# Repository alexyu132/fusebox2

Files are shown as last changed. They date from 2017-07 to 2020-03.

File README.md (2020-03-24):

# FuseBox2/FuseBox2R
A new CoreXY 3D printer design. This design has 2 variants:

* FuseBox2R: An improved version using an MGN12 linear rail gantry.
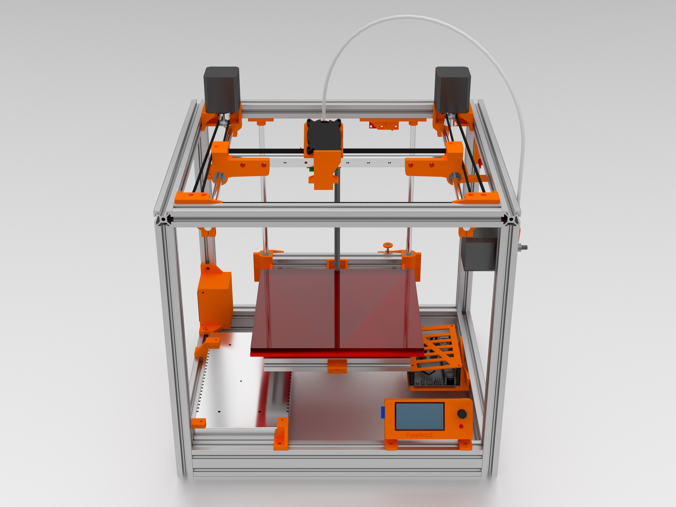
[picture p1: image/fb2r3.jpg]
FuseBox2R Render


* FuseBox2: The original design using a dual 8mm rod gantry.

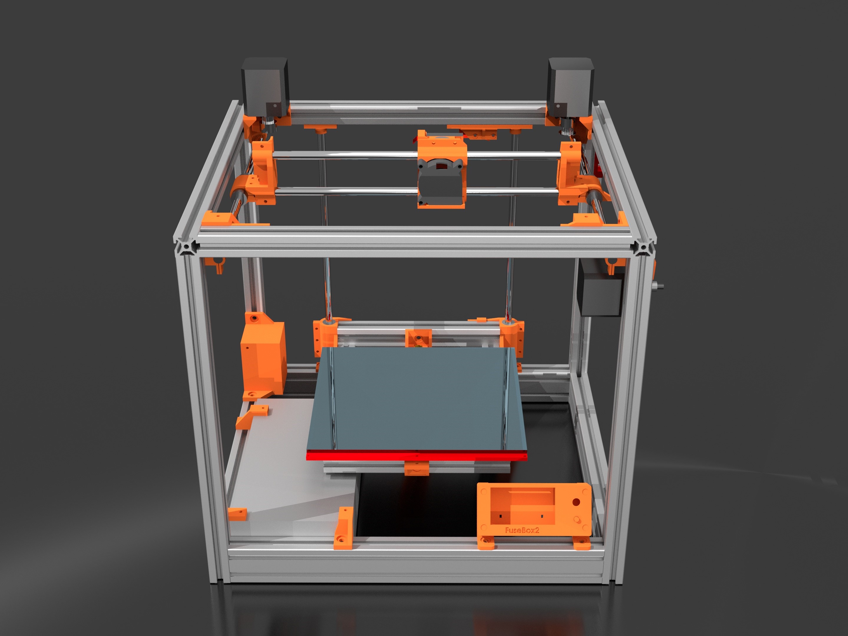
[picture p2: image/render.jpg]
FuseBox2 Render


## Specifications
* Rigid 2020(top and sides)/2040(bottom) aluminum extrusion frame
* Non-crossing CoreXY belt path
* 210x200x210mm (FuseBox2) or 210x205x210mm (FuseBox2R) build area
* 390x340x412mm size
* PCB heatbed with 3 point leveling
* Powerful 2040 part cooling blower
* E3D V6 compatible hotend + Bowden extruder
* 24v + 32 bit electronics recommended - SKR 1.3 and Duet are good options

## Improvements over original FuseBox
* Slightly more compact
* Slightly larger build area
* Much greater frame and z axis rigidity
* Belt tensioning improvements - much easier to tension; screw-clamped to prevent slipping out
* Clamped bearing and rod mounts - no more structural zip ties
* Proper belt idlers instead of 625 bearings - eliminates belt rubbing
* Extrusions (optionally) joined via tapped ends + screws instead of corner brackets
* Lowered part count
* Better endstop mounting

# Variants

## FuseBox2 v1.0.1

* Minor change from 1.0 - added adjustment screw for more precise Z offset adjustment. Eliminates 2 M5x8mm screws and t-nuts, and needs 1 additional M3x25mm (or longer) bolt and 2 additional M3 lock nuts.

## FuseBox2R v1.1
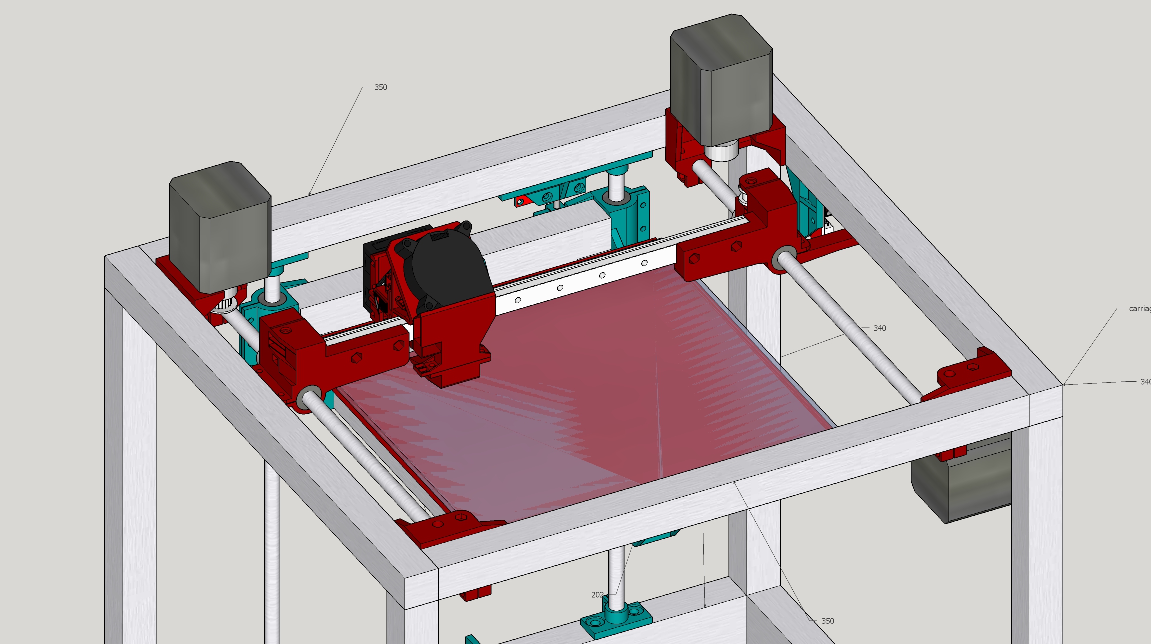
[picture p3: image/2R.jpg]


Switches out the twin 8mm rods on the gantry for a single MGN12 rail. Improvements include 30% gantry weight savings for less ringing and higher speeds, lowered bearing noise, easier belt tensioning, and a modular fan duct. Relatively inexpensive ($10-$15) MGN12 rails can be found on Aliexpress, so it's recommended to build this configuration if starting from scratch. The printed parts for the 2R gantry are in the rail gantry subfolder in the stl folder. Don't print anything from the stock gantry folder if building the rail gantry version, and vice versa.

### Changes from FuseBox2
The entire CoreXY movement will need to be changed out. This includes all the parts on the gantry itself as well as the motor mounts and idler blocks.

Compared to the stock gantry, the belts may need to be shortened slightly.

### Changes in FuseBox2R v1.1

Revised XY movement to simplify assembly and address issues with v1.0 rail gantry:

- X-end rigidity improvements
- Belts moved closer to centerline of MGN rail - alleviates x-end bending from belt tension; should further reduce ringing
- Corner idler brackets made more robust and compact - allows for a few mm more Y travel
- Homing direction reverted to x-min
- Thicker, more rigid 8mm rod holders with looser unclamped fit for easier rod installation

# BOM

| Item | Quantity  |
|---|---|
| **Extrusions**  |
| 2020 extrusion, 350mm | 2  |
| 2020 extrusion, 340mm | 6  |
| 2020 extrusion, 184mm | 1  |
| 2020 extrusion, 202mm | 2  |
| 2040 extrusion, 184mm | 1  |
| 2040 extrusion, 350mm | 2  |
| 2040 extrusion, 300mm | 2  |
| **Heaters, motors, electronics**  |
| MK2 compatible PCB heatbed | 1  |
| Thermistor for heatbed | 1  |
| 15A 24v PSU or 30A 12v PSU | 1  |
| E3DV6 compatible hotend with PTFE tube and coupler | 1  |
| Any electronics (32 bit preferred, mounts available for azsmz board+lcd) | 1  |
| NEMA 17 stepper (60+ oz in/42+ N cm preferred) | 3  |
| NEMA 17 short body stepper (up to 30mm motor body length) | 1  |
| IEC socket with fuse and switch | 1  |
| ~5A 250v fuse | 1  |
| IEC power cord | 1  |
| Mechanical endstop (Note: cut off the microswitch from one endstop to use on the x axis) | 3  |
| 40mm axial fan | 1  |
| 2040 radial blower | 1  |
| **Mechanical**  |
| 8mm OD smooth rod, 300mm length | 6  |
| LM8LUU linear bearing | 6  |
| T8 leadscrew+nut, 250mm length, 2mm pitch preferred | 1  |
| 16T GT2 idler for 6mm belt - 6 toothed/2 smooth (recommended) or all smooth | 8  |
| 20T GT2 pulley for 6mm belt | 2  |
| 3m GT2 belt, 6mm | 1  |
| 625zz bearing | 1  |
| 5mm to 8mm flex coupler | 1  |
| MK8 extruder gear | 1  |
| **Fasteners and other hardware**  |
| M5x8mm button head bolt | 49  |
| M5x12mm button head bolt | 28  |
| M5 T nuts (drop-in recommended) | 49  |
| M3x8mm socket head bolt | 16  |
| M3x10mm button head bolt | 36  |
| M3x25mm button head bolt | 14  |
| Bed leveling spring, nut, and bolt set | 3  |
| Extruder spring | 1  |
| M3 lock nut | 50  |
| Adhesive felt feet | 4  |
| **Misc**  |
| ~200x213mm glass sheet | 1  |
| ~200x213mm PEI sheet with adhesive | 1  |
| Zip ties | Varies  |
| Cable mesh (optional) | Varies  |
| 18AWG wire for AC input | Varies  |
| 14AWG wire for heatbed and main DC power | Varies  |
| Small binder/bulldog clips for bed | 4  |

# FuseBox2R MGN12 upgrade BOM

| Item | Quantity |
|---|---|
| 250mm MGN12 Rail + MGN12C Block |  1 |
| M3x10mm bolt (button head) |  2 |
| M3x6mm bolt (socket head) |  4 |
| M3x10mm bolt (socket head) |  4 |
| M3 lock nut |  1 |
| M3x25mm bolt (button head) | -6 |
| M3x18mm bolt (button head) |  4 |
| 300mm 8mm smooth rod | -2 |
| LM8LUU bearing | -2 |

Note that the upgrade requires new fasteners and parts, but also gets rid of some. If upgrading, get only the positive quantity items. If building from scratch, add item amounts to base BOM.

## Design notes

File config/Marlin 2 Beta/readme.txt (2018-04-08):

These config files are for Marlin 2 with an AZSMZ Mini board. Copy the configuration files into the Marlin directory and the pins file into the src/pins directory.

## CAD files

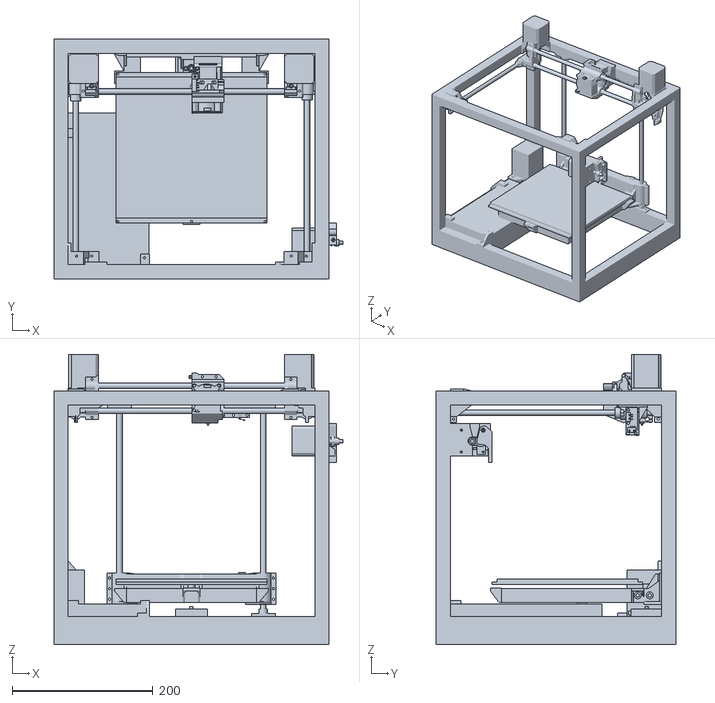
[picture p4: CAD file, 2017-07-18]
FuseBox2.stl
410.0 x 340.0 x 412.0

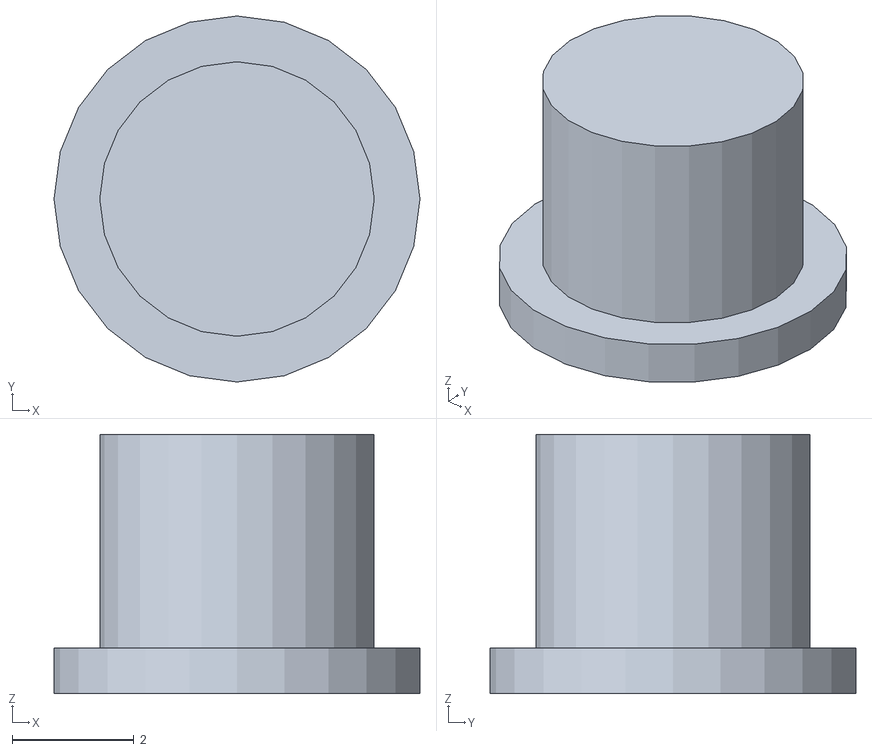
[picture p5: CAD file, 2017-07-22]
stl/Electronics/AZSMZ 12864 LCD/lcd-button.stl
6.00 x 6.00 x 4.25

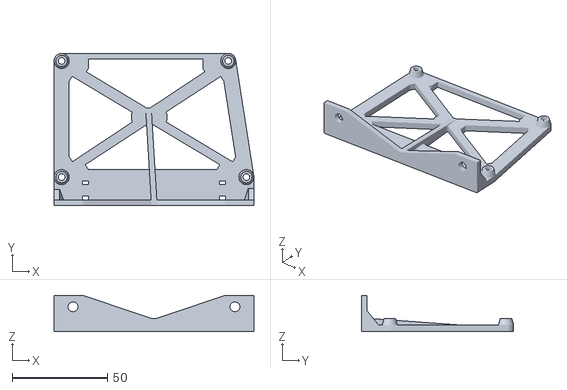
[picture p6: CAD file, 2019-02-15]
stl/Electronics/AZSMZ Mini/azsmz-holder.stl
105.0 x 80.0 x 19.0

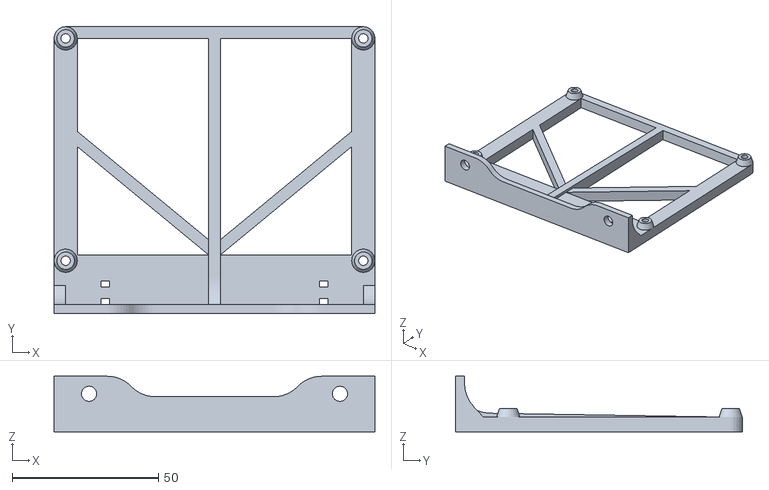
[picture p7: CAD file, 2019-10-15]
stl/Electronics/BigTreeTech SKR 1.3/mount.stl
109.9 x 98.1 x 19.0

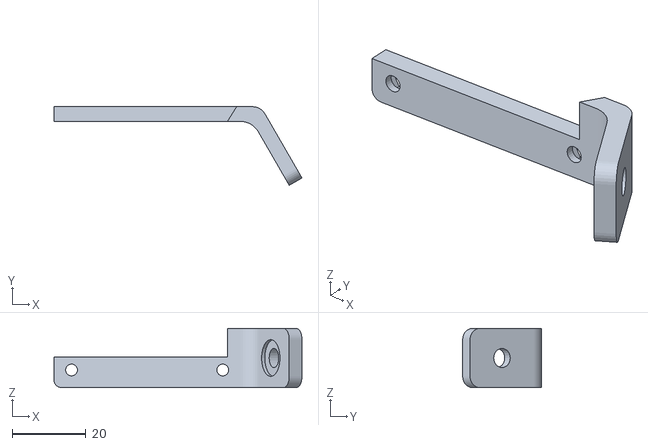
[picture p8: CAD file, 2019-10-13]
stl/Electronics/BigTreeTech TFT24 V1.1/lcd-bracket-left.stl
67.2 x 21.3 x 16.0

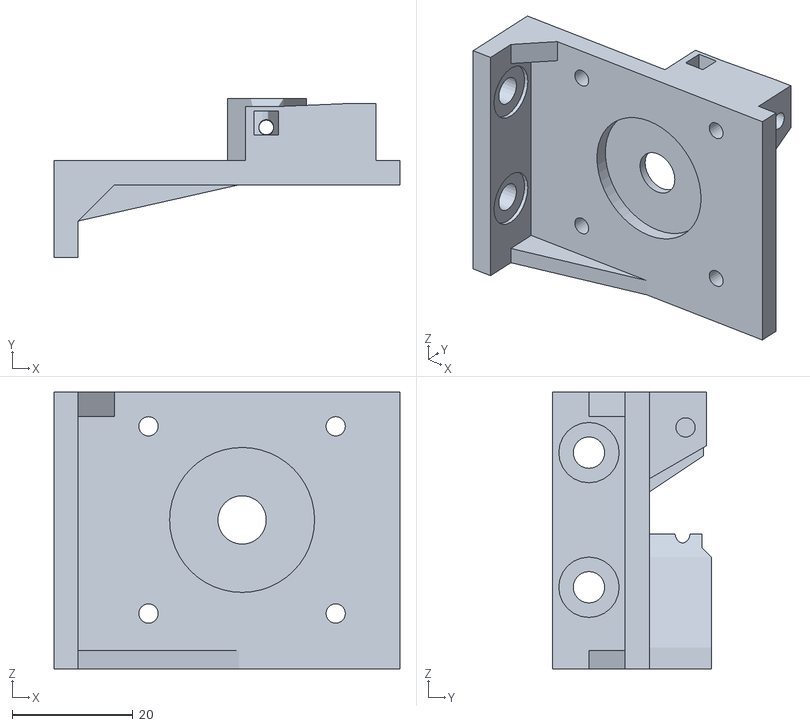
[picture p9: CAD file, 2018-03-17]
stl/Extruder/extruder-body.stl
57.3 x 26.2 x 45.8

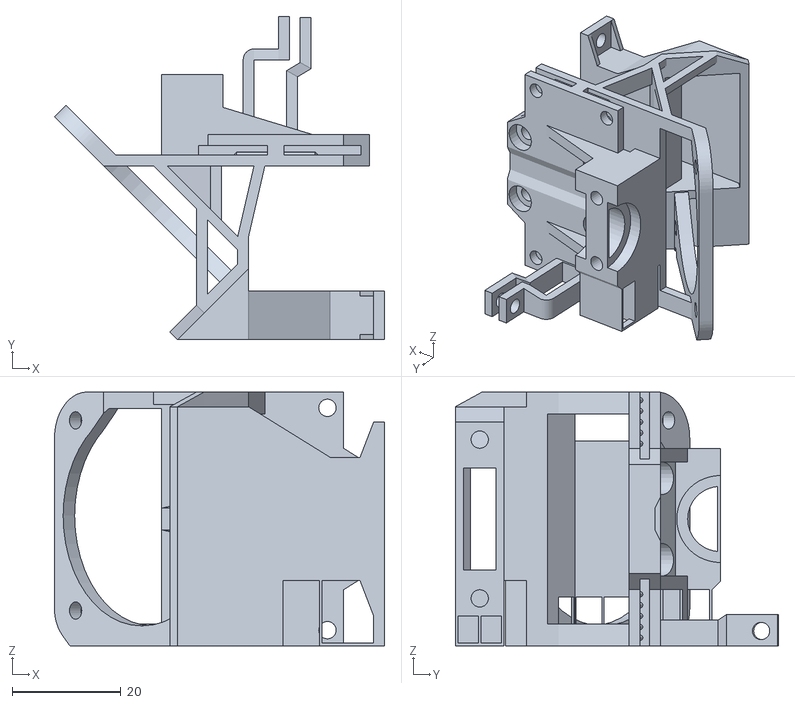
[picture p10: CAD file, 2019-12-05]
stl/Rail Gantry/carriage.stl
60.7 x 59.5 x 46.7

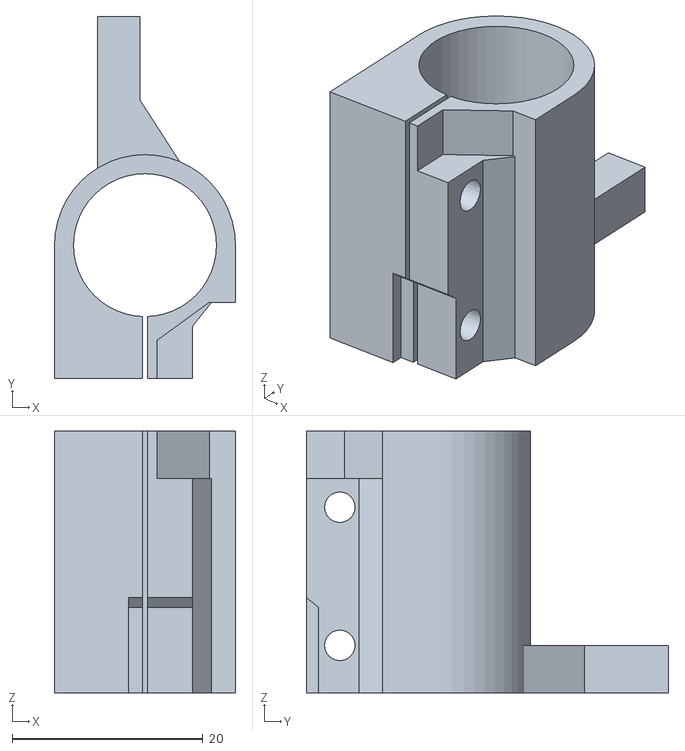
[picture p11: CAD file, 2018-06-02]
stl/Stock Gantry/y-bearing-block-right.stl
19.0 x 38.0 x 27.5

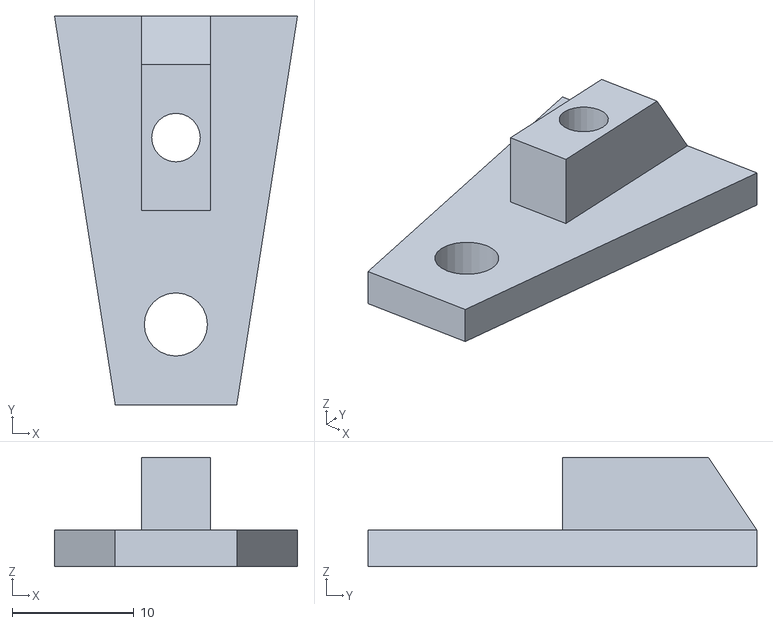
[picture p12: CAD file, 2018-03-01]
stl/Tools/alignment-jig.stl
20.0 x 32.0 x 9.00

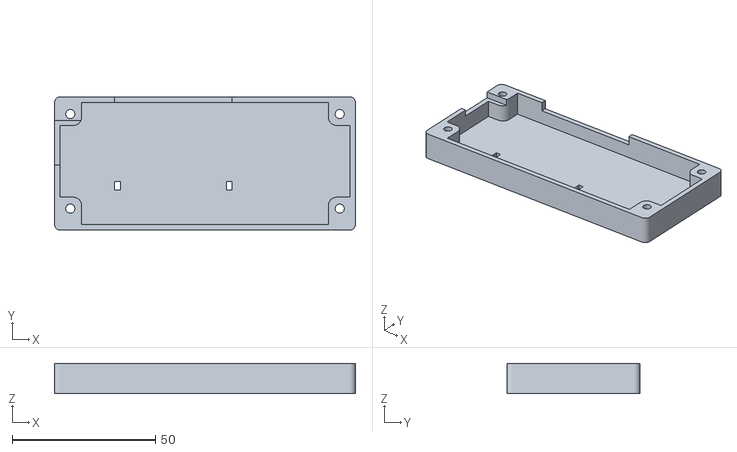
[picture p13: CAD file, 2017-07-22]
stl/Electronics/AZSMZ 12864 LCD/lcd-rear.stl
105.0 x 46.5 x 10.5

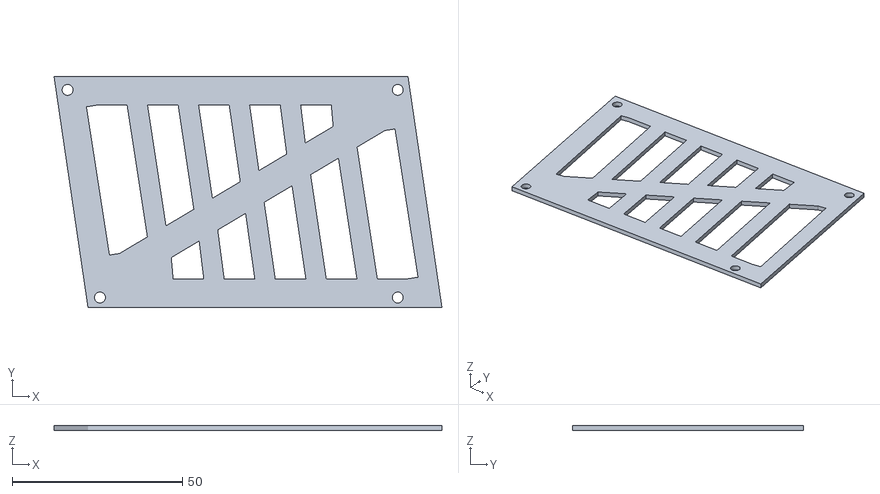
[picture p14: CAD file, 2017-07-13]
stl/Electronics/AZSMZ Mini/azsmz-cover.stl
114.0 x 68.0 x 1.50

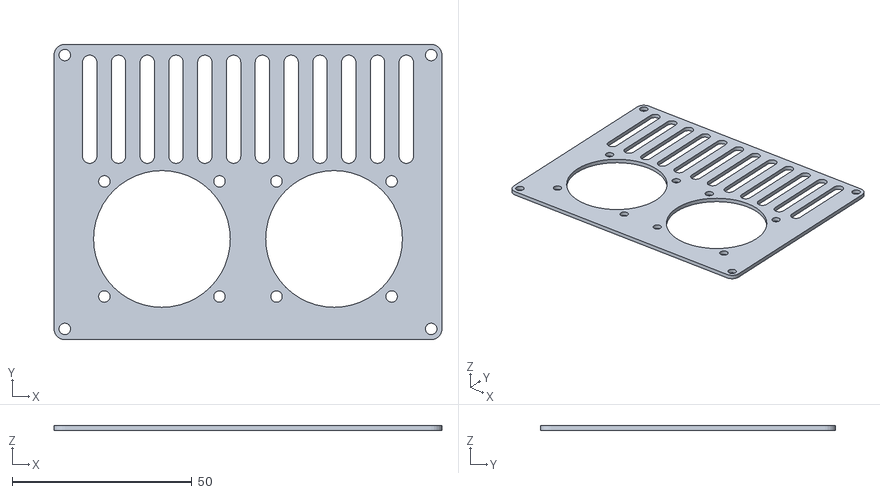
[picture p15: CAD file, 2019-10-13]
stl/Electronics/BigTreeTech SKR 1.3/cover.stl
107.9 x 82.1 x 1.50

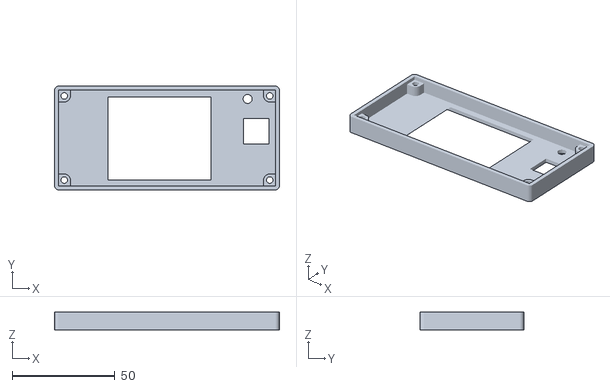
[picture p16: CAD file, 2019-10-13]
stl/Electronics/BigTreeTech TFT24 V1.1/lcd-bezel.stl
109.5 x 50.5 x 8.75

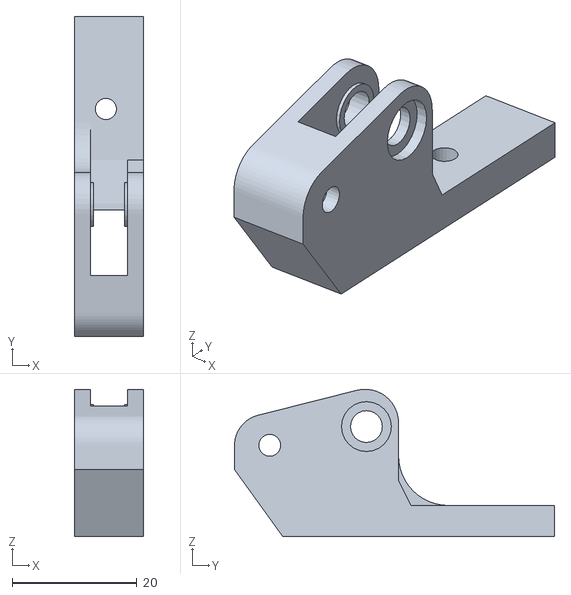
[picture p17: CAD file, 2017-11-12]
stl/Extruder/extruder-arm.stl
11.0 x 51.3 x 23.6

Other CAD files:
stl/Rail Gantry/idler-spacer.stl
stl/Stock Gantry/y-bearing-block-left.stl
stl/Tools/alignment-jig-2040.stl
stl/z-endstop-adjuster.stl
stl/Electronics/AZSMZ 12864 LCD/lcd-bezel.stl
stl/Electronics/AZSMZ 12864 LCD/lcd-bracket-left.stl
stl/Electronics/AZSMZ 12864 LCD/lcd-bracket-right.stl
stl/Electronics/BigTreeTech TFT24 V1.1/lcd-bracket-right.stl
stl/Electronics/BigTreeTech TFT24 V1.1/lcd-rear.stl
stl/Extruder/extruder-pin.stl
stl/Rail Gantry/hotend-block-outer.stl
stl/Rail Gantry/hotend-fan-shroud.stl
stl/Rail Gantry/idler-mount-left.stl
stl/Rail Gantry/idler-mount-right.stl
stl/Rail Gantry/motor-mount-left.stl
stl/Rail Gantry/motor-mount-right.stl
stl/Rail Gantry/print-cooling-duct-a.stl
stl/Rail Gantry/print-cooling-duct-b.stl
stl/Rail Gantry/x-end-left.stl
stl/Rail Gantry/x-end-right.stl
stl/Stock Gantry/carriage.stl
stl/Stock Gantry/hotend-block-inner.stl
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

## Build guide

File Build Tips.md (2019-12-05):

# Tools

* M3 and M5 hex keys
* Pliers
* 3mm wrench
* Power drill with ~5mm bit
* M5 tap

# Print settings
### Resolution

0.2mm or less

### Infill

25-30% is sufficient for most structural parts, but the x-ends, z bearing blocks, and carriage should be a bit more (35-50%). Infill can be lower for non-structural parts like the display enclosure, y-axis endstop holder, and plug box.

### Shells

At least 1.2-1.6mm thick (3-4 perimeters on a 0.4mm nozzle) for structural parts. X-ends, z bearing blocks, and carriage should use 1.6-2.0mm thickness (4-5 perimeters).

### Supports

Off for everything. Make sure your printer has good cooling, as many parts require good bridging abilities.

### Material

For most of the parts, PLA, PETG, ABS, and similar filaments are fine. ABS or PETG should be used for the hotend cooling shroud. If your motors get hot, use these filaments for the motor mounts as well.

# Print finishing and support removal

Make sure to get rid of stringing or other rough areas where the linear bearings and rods are mounted to make installing those parts easier. Some parts may have a tight fit depending on your printer. To loosen up the linear rod holders, you can chuck a smooth rod in a drill and run it through the holder pieces - it'll take a bit of plastic off the inside.

The parts are designed to not require slicer-generated supports. However, some parts include built-in supports that should be removed. Needlenose pliers are ideal for this task.

## X-ends
For the FuseBox2R, each x-end has 2 thin strips of support where one of the idler pulleys and its belt is supposed to fit. Remove these using pliers and make sure there is no remaining material that could scrape the belt.

## Carriage
For the FuseBox2, there is a strip of plastic underneath the fan duct that can be torn off by hand.

For the FuseBox2R, there are more supports that need to be removed. Probably best to show with a picture:

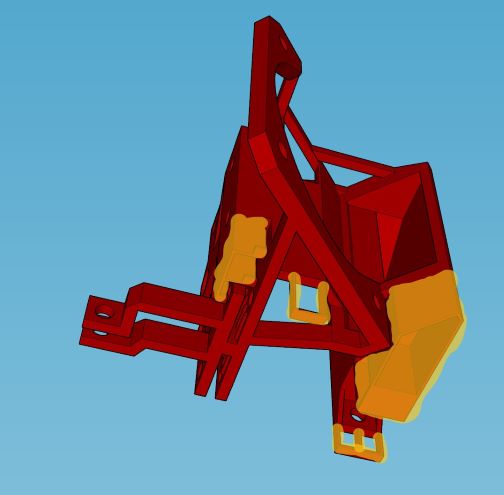
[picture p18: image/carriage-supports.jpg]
FuseBox2R carriage support removal


# Joining extrusions

FuseBox2 optionally does away with corner brackets and instead uses a tap and drill method to join the extrusions - this results in a lower part count, a cleaner appearance, and likely greater rigidity. You can also use corner brackets, but if you have the tools and the time, tapping and drilling is recommended. If using corner brackets, you can replace the bottom 2040 extrusions with 2020 to reduce cost a bit.

To connect 2 extrusions perpendicularly, use an M5 tap to tap the end of the first extrusion. On the second extrusion, drill an access hole where you want the first extrusion to connect. Partially screw in a 12mm M5 bolt to the end of the first extrusion, and slip the bolt head into the channel of the second extrusion. Tighten down to attach the pieces rigidly together.

A more detailed explanation of how to connect extrusions using this method is available [here.](http://forums.reprap.org/read.php?177,601562)

# Assembly notes

## Frame

It is recommended to use the drilling and tapping technique described above to join the extrusions. Use the M5x12mm bolts for this. The extrusion lengths are shown below:

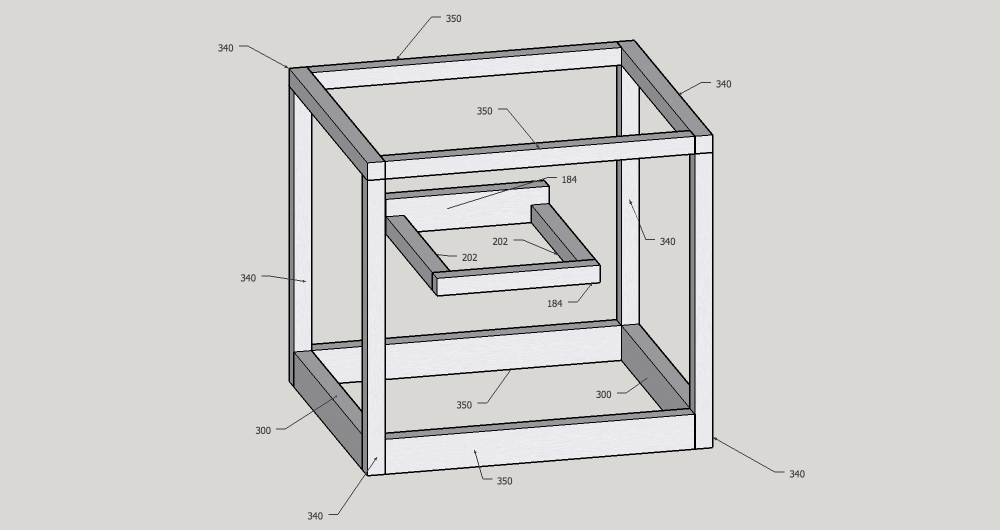
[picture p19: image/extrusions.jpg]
Extrusion lengths


Following frame assembly, you can either work on the gantry assembly or the z-axis.

## Motor mounts and idler blocks

Attach the motor mounts and idler blocks onto the frame using the M5x8mm bolts and t-slot nuts.

To install the idler pulleys into the blocks, first place a spacer in position according to the images below. Partially insert an M3x25mm bolt from the spacer side until it is flush with the exposed end of the spacer. Then insert the idler pulley into position and push the bolt all the way through. Tighten down using a lock nut on the opposite side.

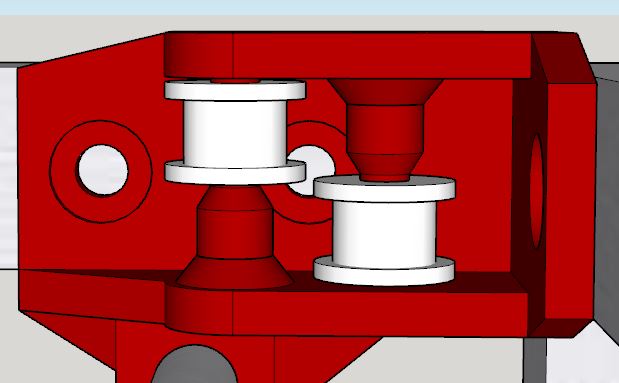
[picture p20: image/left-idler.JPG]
Left idler

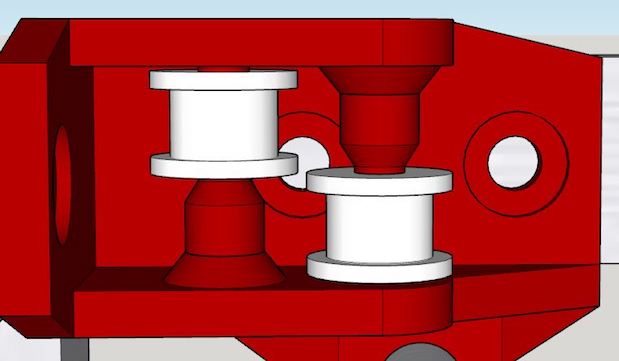
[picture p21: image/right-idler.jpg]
Right idler


## Gantry assembly

Install the idler pulleys in each x-end using either a single M3x25mm bolt (dual rod gantry) or dual M3x18mm bolts (rail gantry). Then insert the linear bearings in the x-ends (rail gantry) or y bearing blocks (dual rod gantry). Note that for each of the rail gantry's x-ends, one of the idler pulley bolts goes in through where the linear bearing will be, so it must be installed before the bearing is inserted.

With the dual rod gantry, join the y bearing blocks with the x-ends using M3x25mm bolts and tighten down. Install the bearings in the carriage. Then insert two 8mm rods into one x-end and slip the carriage onto the rods, making sure it isn't backwards. Then put the remaining x-end on the other end of the rods.

The assembly process for the rail gantry is much easier. Use 4 M3x10mm socket head bolts and lock nuts to attach the rail to each x-end. Use 4 M3x6mm socket head bolts to attach the carriage to the rail. Dual M3x10mm button head bolts on each end are used to tighten down the linear bearings.

## Attaching the gantry

Insert the y rods into the idler blocks from the front of the machine and stop when about halfway through. Then slip the assembled gantry onto the rods. Then push the y rods all the way through to the motor mounts, and tighten each rod mounting point using an M3x10mm bolt. For the rail gantry, it is helpful to loosen the connection between the x-ends and the rail and tighten after the gantry is installed on the y rods.

## Belt attachment

TODO

## Carriage

TODO

## Z-Axis

TODO

## Electronics

TODO

# Fan duct options

FuseBox2R includes 2 cooling duct options:

## print-cooling-duct-a.stl

This is a conventional single-exit duct that directs air directly toward the area being printed.

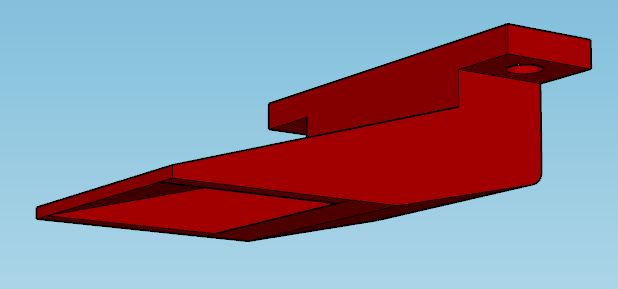
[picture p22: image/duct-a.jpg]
Duct A


## print-cooling-duct-b.stl

This is an experimental dual-exit duct that directs air toward the nozzle from opposite sides. Cooling may be more uniform but airflow is likely slightly less than the other duct. Before installing this duct, remove the support towers on each side.

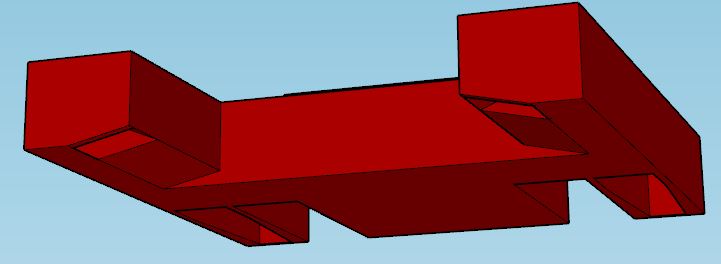
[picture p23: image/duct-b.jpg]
Duct B


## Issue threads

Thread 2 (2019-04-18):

confused belt system?

kevinshane, 2019-04-18:
Hi sir, very nice job for the printer, I am building it. however the belt system confuse me a lot and there is no other reference except for just 1 or 2 images, I can't figure it out how they connect to each other, would you please upload some pic for the rear view or maybe the best is adding the belts to sketchup file, thanks!

007foryou, 2019-06-08:
nice to meet you ,you could look  coreXY on google

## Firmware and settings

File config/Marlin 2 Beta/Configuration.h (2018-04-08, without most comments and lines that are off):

#define CONFIGURATION_H
#define CONFIGURATION_H_VERSION 020000
#define STRING_CONFIG_H_AUTHOR "(none, default config)" // Who made the changes.
#define SHOW_BOOTSCREEN
#define STRING_SPLASH_LINE1 SHORT_BUILD_VERSION // will be shown during bootup in line 1
#define STRING_SPLASH_LINE2 WEBSITE_URL         // will be shown during bootup in line 2
#define SERIAL_PORT 0
#define SERIAL_PORT_2 -1
#define BAUDRATE 115200
  #define MOTHERBOARD BOARD_AZSMZ_MINI
#define CUSTOM_MACHINE_NAME "FuseBox2"
#define EXTRUDERS 1
#define DEFAULT_NOMINAL_FILAMENT_DIA 1.75
#define POWER_SUPPLY 0
#define TEMP_SENSOR_0 5
#define TEMP_SENSOR_1 0
#define TEMP_SENSOR_2 0
#define TEMP_SENSOR_3 0
#define TEMP_SENSOR_4 0
#define TEMP_SENSOR_BED 11
#define DUMMY_THERMISTOR_998_VALUE 25
#define DUMMY_THERMISTOR_999_VALUE 100
#define MAX_REDUNDANT_TEMP_SENSOR_DIFF 10
#define TEMP_RESIDENCY_TIME 8  // (seconds)
#define TEMP_HYSTERESIS 3       // (degC) range of +/- temperatures considered "close" to the target one
#define TEMP_WINDOW     1       // (degC) Window around target to start the residency timer x degC early.
#define TEMP_BED_RESIDENCY_TIME 8  // (seconds)
#define TEMP_BED_HYSTERESIS 3       // (degC) range of +/- temperatures considered "close" to the target one
#define TEMP_BED_WINDOW     1       // (degC) Window around target to start the residency timer x degC early.
#define HEATER_0_MINTEMP 5
#define HEATER_1_MINTEMP 5
#define HEATER_2_MINTEMP 5
#define HEATER_3_MINTEMP 5
#define HEATER_4_MINTEMP 5
#define BED_MINTEMP 5
#define HEATER_0_MAXTEMP 275
#define HEATER_1_MAXTEMP 275
#define HEATER_2_MAXTEMP 275
#define HEATER_3_MAXTEMP 275
#define HEATER_4_MAXTEMP 275
#define BED_MAXTEMP 120
#define PIDTEMP
#define BANG_MAX 255     // Limits current to nozzle while in bang-bang mode; 255=full current
#define PID_MAX BANG_MAX // Limits current to nozzle while PID is active (see PID_FUNCTIONAL_RANGE below); 255=full current
#define PID_K1 0.95      // Smoothing factor within any PID loop
  #define PID_FUNCTIONAL_RANGE 10 // If the temperature difference between the target temperature and the actual temperature
  #define  DEFAULT_Kp 17.540509
  #define  DEFAULT_Ki 2.345459
  #define  DEFAULT_Kd 33.606663
#define PIDTEMPBED
#define MAX_BED_POWER 255 // limits duty cycle to bed; 255=full current
  #define  DEFAULT_bedKp 85.0418
  #define  DEFAULT_bedKi 5.783129
  #define  DEFAULT_bedKd 436.981934
#define PREVENT_COLD_EXTRUSION
#define EXTRUDE_MINTEMP 170
#define PREVENT_LENGTHY_EXTRUDE
#define EXTRUDE_MAXLENGTH 200
#define THERMAL_PROTECTION_HOTENDS // Enable thermal protection for all extruders
#define THERMAL_PROTECTION_BED     // Enable thermal protection for the heated bed
#define COREXY
#define USE_XMIN_PLUG
#define USE_ZMIN_PLUG
#define USE_YMAX_PLUG
#define ENDSTOPPULLUPS // Comment this out (using // at the start of the line) to disable the endstop pullup resistors
#define X_MIN_ENDSTOP_INVERTING false // set to true to invert the logic of the endstop.
#define Y_MIN_ENDSTOP_INVERTING false // set to true to invert the logic of the endstop.
#define Z_MIN_ENDSTOP_INVERTING true // set to true to invert the logic of the endstop.
#define X_MAX_ENDSTOP_INVERTING false // set to true to invert the logic of the endstop.
#define Y_MAX_ENDSTOP_INVERTING true // set to true to invert the logic of the endstop.
#define Z_MAX_ENDSTOP_INVERTING false // set to true to invert the logic of the endstop.
#define Z_MIN_PROBE_ENDSTOP_INVERTING false // set to true to invert the logic of the probe.
#define DEFAULT_AXIS_STEPS_PER_UNIT   { 80, 80, 1600, 1143 }
#define DEFAULT_MAX_FEEDRATE          { 300, 300, 5, 100 }
#define DEFAULT_MAX_ACCELERATION      { 4000, 4000, 500, 9000 }
#define DEFAULT_ACCELERATION          4000    // X, Y, Z and E acceleration for printing moves
#define DEFAULT_RETRACT_ACCELERATION  4000    // E acceleration for retracts
#define DEFAULT_TRAVEL_ACCELERATION   4000    // X, Y, Z acceleration for travel (non printing) moves
#define DEFAULT_XJERK                 12.0
#define DEFAULT_YJERK                 12.0
#define DEFAULT_ZJERK                  0.3
#define DEFAULT_EJERK                  5.0
#define Z_MIN_PROBE_USES_Z_MIN_ENDSTOP_PIN
#define X_PROBE_OFFSET_FROM_EXTRUDER 10  // X offset: -left  +right  [of the nozzle]
#define Y_PROBE_OFFSET_FROM_EXTRUDER 10  // Y offset: -front +behind [the nozzle]
#define Z_PROBE_OFFSET_FROM_EXTRUDER 0   // Z offset: -below +above  [the nozzle]
#define XY_PROBE_SPEED 8000
#define Z_PROBE_SPEED_FAST HOMING_FEEDRATE_Z
#define Z_PROBE_SPEED_SLOW (Z_PROBE_SPEED_FAST / 2)
#define Z_CLEARANCE_DEPLOY_PROBE   10 // Z Clearance for Deploy/Stow
#define Z_CLEARANCE_BETWEEN_PROBES  5 // Z Clearance between probe points
#define Z_PROBE_OFFSET_RANGE_MIN -20
#define Z_PROBE_OFFSET_RANGE_MAX 20
#define X_ENABLE_ON 0
#define Y_ENABLE_ON 0
#define Z_ENABLE_ON 0
#define E_ENABLE_ON 0 // For all extruders
#define DISABLE_X false
#define DISABLE_Y false
#define DISABLE_Z false
#define DISABLE_E false // For all extruders
#define DISABLE_INACTIVE_EXTRUDER true // Keep only the active extruder enabled.
#define INVERT_X_DIR true
#define INVERT_Y_DIR true
#define INVERT_Z_DIR true
#define INVERT_E0_DIR true
#define INVERT_E1_DIR false
#define INVERT_E2_DIR false
#define INVERT_E3_DIR false
#define INVERT_E4_DIR false
#define X_HOME_DIR -1
#define Y_HOME_DIR 1
#define Z_HOME_DIR -1
#define X_BED_SIZE 210
#define Y_BED_SIZE 205
#define X_MIN_POS 0
#define Y_MIN_POS 0
#define Z_MIN_POS 0
#define X_MAX_POS X_BED_SIZE
#define Y_MAX_POS Y_BED_SIZE
#define Z_MAX_POS 210
#define MIN_SOFTWARE_ENDSTOPS
  #define MIN_SOFTWARE_ENDSTOP_X
  #define MIN_SOFTWARE_ENDSTOP_Y
  #define MIN_SOFTWARE_ENDSTOP_Z
#define MAX_SOFTWARE_ENDSTOPS
  #define MAX_SOFTWARE_ENDSTOP_X
  #define MAX_SOFTWARE_ENDSTOP_Y
  #define MAX_SOFTWARE_ENDSTOP_Z
#define MANUAL_X_HOME_POS -5
#define MANUAL_Y_HOME_POS 205
#define HOMING_FEEDRATE_XY (50*60)
#define HOMING_FEEDRATE_Z  (4*60)
#define EEPROM_CHITCHAT   // Give feedback on EEPROM commands. Disable to save PROGMEM.
#define HOST_KEEPALIVE_FEATURE        // Disable this if your host doesn't like keepalive messages
#define DEFAULT_KEEPALIVE_INTERVAL 2  // Number of seconds between "busy" messages. Set with M113.
#define BUSY_WHILE_HEATING            // Some hosts require "busy" messages even during heating
#define PREHEAT_1_TEMP_HOTEND 180
#define PREHEAT_1_TEMP_BED     70
#define PREHEAT_1_FAN_SPEED     0 // Value from 0 to 255
#define PREHEAT_2_TEMP_HOTEND 240
#define PREHEAT_2_TEMP_BED    110
#define PREHEAT_2_FAN_SPEED     0 // Value from 0 to 255
#define PRINTJOB_TIMER_AUTOSTART
#define LCD_LANGUAGE en
#define DISPLAY_CHARSET_HD44780 JAPANESE
#define DOGLCD      // Full graphics display
#define SDSUPPORT
#define INDIVIDUAL_AXIS_HOMING_MENU
#define AZSMZ_12864
#define SOFT_PWM_SCALE 0
#define SERVO_DELAY { 300 }

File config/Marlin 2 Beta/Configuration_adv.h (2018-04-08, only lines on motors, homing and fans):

#define E0_AUTO_FAN_PIN P0_26
#define E1_AUTO_FAN_PIN -1
#define E2_AUTO_FAN_PIN -1
#define E3_AUTO_FAN_PIN -1
#define E4_AUTO_FAN_PIN -1
#define X_HOME_BUMP_MM 5
#define Y_HOME_BUMP_MM 5
#define Z_HOME_BUMP_MM 2
#define HOMING_BUMP_DIVISOR { 2, 2, 4 }  // Re-Bump Speed Divisor (Divides the Homing Feedrate)
#define HOME_Y_BEFORE_X
#define MICROSTEP_MODES {16,16,16,16,16} // [1,2,4,8,16]
#define DIGIPOT_I2C_MOTOR_CURRENTS { 1.0, 1.0, 1.0, 1.0, 1.0, 1.0, 1.0, 1.0 }  //  AZTEEG_X3_PRO

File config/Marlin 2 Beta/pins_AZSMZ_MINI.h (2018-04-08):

/**
 * Marlin 3D Printer Firmware
 * Copyright (C) 2017 MarlinFirmware [https://github.com/MarlinFirmware/Marlin]
 *
 * Based on Sprinter and grbl.
 * Copyright (C) 2011 Camiel Gubbels / Erik van der Zalm
 *
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
 */

/**
 * AZSMZ MINI pin assignments
 */

#ifndef TARGET_LPC1768
  #error "Oops!  Make sure you have LPC1768 selected."
#endif

#ifndef BOARD_NAME
  #define BOARD_NAME "AZSMZ MINI"
#endif

//
// Servos
//
#define SERVO0_PIN         P1_23

//
// Limit Switches
//
#define X_MIN_PIN          P1_24
#define Y_MAX_PIN          P1_26
#define Z_MIN_PIN          P1_28
#define Z_MAX_PIN          P1_29

//
// Steppers
//
#define Y_STEP_PIN         P2_00
#define Y_DIR_PIN          P0_05
#define Y_ENABLE_PIN       P0_04

#define X_STEP_PIN         P2_01
#define X_DIR_PIN          P0_11
#define X_ENABLE_PIN       P0_10

#define Z_STEP_PIN         P2_02
#define Z_DIR_PIN          P0_20
#define Z_ENABLE_PIN       P0_19

#define E0_STEP_PIN        P2_03
#define E0_DIR_PIN         P0_22
#define E0_ENABLE_PIN      P0_21

#define E1_STEP_PIN        P2_08
#define E1_DIR_PIN         P2_13
#define E1_ENABLE_PIN      P4_29

//
// Temperature Sensors
//  3.3V max when defined as an analog input
//
#define TEMP_0_PIN          0  // A0 (TH1)
#define TEMP_BED_PIN        2  // A1 (TH2)
#define TEMP_1_PIN          1  // A2 (TH3)

//
// Heaters / Fans
//
// EFB
#define HEATER_0_PIN       P2_04
#define HEATER_BED_PIN     P2_05
#define FAN_PIN            P2_07
#define FAN1_PIN           P0_26

#if ENABLED(AZSMZ_12864)
  #define BEEPER_PIN       P1_30
  #define DOGLCD_A0        P2_06
  #define DOGLCD_CS        P1_22
  #define BTN_EN2          P4_28
  #define BTN_EN1          P1_27
  #define BTN_ENC          P3_26
  #define LCD_SDSS         P0_16
  #define SD_DETECT_PIN    P3_25
#endif

//
// Ethernet pins
//
#define ENET_MDIO          P1_17
#define ENET_RX_ER         P1_14
#define ENET_RXD1          P1_10
#define ENET_MOC           P1_16
#define REF_CLK            P1_15
#define ENET_RXD0          P1_09
#define ENET_CRS           P1_08
#define ENET_TX_EN         P1_04
#define ENET_TXD0          P1_00
#define ENET_TXD1          P1_01

/**
 *  PWMs
 *
 *  There are 6 PWMs.  Each PWM can be assigned to one of two pins.
 *
 *  SERVO2 does NOT have a PWM assigned to it.
 *
 *  PWM1.1   DIO4    SERVO3_PIN       FIL_RUNOUT_PIN   5V output, PWM
 *  PWM1.1   DIO26   E0_STEP_PIN
 *  PWM1.2   DIO11   SERVO0_PIN
 *  PWM1.2   DIO54   X_STEP_PIN
 *  PWM1.3   DIO6    SERVO1_PIN       J5-1
 *  PWM1.3   DIO60   Y_STEP_PIN
 *  PWM1.4   DIO53   SDSS(SSEL0)      J3-5  AUX-3
 *  PWM1.4   DIO46   Z_STEP_PIN
 *  PWM1.5   DIO3    X_MIN_PIN        10K PULLUP TO 3.3v, 1K SERIES
 *  PWM1.5   DIO9    RAMPS_D9_PIN
 *  PWM1.6   DIO14   Y_MIN_PIN        10K PULLUP TO 3.3v, 1K SERIES
 *  PWM1.6   DIO10   RAMPS_D10_PIN
 */

 /**
  * Special pins
  *   D37 - not 5V tolerant
  *   D49 - not 5V tolerant
  *   D57 - open collector
  *   D58 - open collector
  */

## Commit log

2017-06-17 Belt attachment tweaks; strength improvement
2017-06-18 Printability improvement
2017-06-29 Ease of assembly tweaks
2017-07-04 Fix endstop mounts, adjust some tolerances
2017-07-08 Add whole printer stl, reinforce x ends and increase clearances for print fan
    [FuseBox2.stl]
2017-07-09 Add extruder
    [FuseBox2.stl]
2017-07-13 Add stl files, improve extruder
    [azsmz-cover.stl, azsmz-holder.stl, bed-mount-center-front.stl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]
2017-07-14 Fix slight misalignment in extruder pin
    [extruder-pin.stl]
2017-07-15 PSU bracket design
2017-07-17 Add power supply mounts
    [power-socket-mount-1.stl, power-socket-mount-2.stl, psu-mount.stl]
2017-07-18 Clean up skp, add alignment jig stl
    [alignment-jig.stl]
2017-07-18 Update whole printer stl
    [FuseBox2.stl]
2017-07-22 Add lcd mounting hardware
    [lcd-bezel.stl, lcd-bracket-left.stl, lcd-bracket-right.stl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]
2017-07-22 Fix lcd front bezel
    [lcd-bezel.stl, lcd-button.stl, lcd-rear.stl]
2017-07-29 Fix mirroring error in right x end
    [x-end-right.stl]
2017-08-11 Fix center bed mount stl
    [bed-mount-center-front.stl]
2017-08-11 Add BOM to readme
2017-11-12 Modify arm for increased tension
    [extruder-arm.stl]
2018-01-23 Strengthen x-ends to reduce gantry twisting
    [x-end-left.stl, x-end-right.stl, y-bearing-block-left.stl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]
2018-01-24 Fix stl name
    [y-bearing-block-right.stl, z-bearing-block-right.stl, z_bearing_block_right.stl]
2018-03-01 Add alignment jig for 2040 extrusions
    [alignment-jig-2040.stl]
2018-03-01 Fix new alignment jig, decrease clearances
    [alignment-jig-2040.stl, alignment-jig.stl]
2018-03-16 Modify extruder for flexible filaments
    [extruder-body.stl]
2018-03-17 Extruder fix
    [extruder-body.stl]
2018-03-17 Increase coupler bore
    [extruder-body.stl]
2018-04-08 Add Marlin config files
    [Configuration.h, Configuration_adv.h]
2018-05-18 Socket mount curved edges, carriage filament savings, remove hotend duct air leak
    [carriage.stl, hotend-fan-duct.stl, power-socket-mount-1.stl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]
2018-05-19 Tidy up, strengthen gantry attachment points
    [x-end-left.stl, x-end-right.stl, y-bearing-block-left.stl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]
2018-05-30 Thicken top bearing clamp on carriage
    [carriage.stl]
2018-06-02 Increase clamping screw spacing on x-ends, cleanup
    [x-end-left.stl, x-end-right.stl, y-bearing-block-left.stl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]
2018-06-23 Add experimental rail gantry file
2018-06-25 Add x endstop and fan mount to carriage
2018-06-25 Add nut inserts for carriage belt clamps
2018-06-30 Compact gantry, 1.5mm z travel increase
2018-07-14 Bolt spacing on xy motor mounts
2018-07-14 Shortened bed mounts, compact version of 2R
    Compact version of 2R (9mm less wide)
    Bed mounts reduced in height for greater z travel
    [bed-mount-center-front.stl, bed-mount-rear-left.stl, bed-mount-rear-right.stl]
2018-07-14 Tweak 2R motor mount height
2018-07-19 Strengthen idlers
2018-07-20 carriage fix
2018-07-21 idler, motor mount fix/improvements
2018-07-21 carriage error fix
2018-07-21 fix fan clearance
2018-07-21 extruder fan duct tweak
2018-07-22 add y endstop presser
2018-07-22 increase y rod holder tolerance for easier installation
2018-07-22 Export STLs and update readme for 2R upgrade
    [carriage.stl, hotend-block-inner.stl, hotend-block-outer.stl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]
2018-07-30 FuseBox2R: strengthen x ends
    [x-end-left.stl, x-end-right.stl]
2018-07-30 [2R] fix hotend fan duct
    [hotend-fan-duct.stl]
2018-11-04 small tweaks
    [hotend-fan-duct-new.stl, x-end-left.stl, x-end-right.stl]
2018-11-07 initial 2R gantry v2
2018-11-10 new carriage
2018-11-17 update experimental rail
2018-11-17 R-gantry motor mount improvements
    [motor-mount-left.stl, motor-mount-right.stl]
2018-11-24 new gantry fan duct
2018-12-03 Update carriage
2018-12-03 Add fan duct
2018-12-05 change belt clamps, x-ends
2018-12-06 Fixes, add y endstop bar
2018-12-06 adjust fan duct mount
2018-12-18 thicker idler spacers
2018-12-19 motor mount screw access holes
2018-12-22 Prototype fixes
    Various clearances adjusted, 2mm extra belt tensioning space per side
2018-12-23 Add simple cooling duct
2018-12-25 screw-adjusted z endstop
2018-12-25 Add build tips, tweak idler blocks, organize 2R skp file, export stls, update readme
    [carriage.stl, hotend-block-inner.stl, hotend-block-outer.stl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]
2018-12-25 Update readme and build guide; additional mounting screw engagement for carriage
    [carriage.stl]
2018-12-26 Update readme, tweak idler blocks
    [idler-mount-left.stl, idler-mount-right.stl]
2018-12-29 Tweak fan duct A angle, update readme
    [print-cooling-duct-a.stl]
2019-02-15 Fix clearances for AZSMZ mount
    [azsmz-holder.stl]
2019-02-18 add fusebox2r render
2019-04-29 tweak fan duct
2019-09-22 Tweak carriage for additional strength
    [carriage.stl]
2019-09-22 Slightly increase idler spacer screw hole size for easier installation
    [idler-spacer.stl]
2019-09-28 Combine inner hotend block and carriage, round out some edges on fan shroud
    [carriage.stl, hotend-block-inner.stl, hotend-block-outer.stl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]
2019-10-13 Reorganize STL directory, add SKR, TFT cases
    [alignment-jig-2040.stl, alignment-jig.stl, azsmz-cover.stl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]
2019-10-15 Increase wire routing space for SKR mount
    [mount.stl]
2019-11-30 Increase carriage support footprint for better bed adhesion
    [carriage.stl]
2019-12-05 Increase clearances for idler spacers and print fan mount
    [carriage.stl, idler-spacer.stl]

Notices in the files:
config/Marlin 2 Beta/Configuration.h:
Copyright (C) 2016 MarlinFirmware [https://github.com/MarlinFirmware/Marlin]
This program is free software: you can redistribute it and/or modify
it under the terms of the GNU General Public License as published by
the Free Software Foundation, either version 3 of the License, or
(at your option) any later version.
